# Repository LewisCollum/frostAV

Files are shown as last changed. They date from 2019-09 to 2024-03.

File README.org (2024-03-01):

Check out [[https://youtu.be/KNiY2aC7Y0c][youtube]], [[https://photos.app.goo.gl/i7FG5oYFuoorvApo9][images]], [[file:org/README.pdf][paper]]

** Getting Started
You do not need a vehicle to get started. As long as you have a
camera/webcam and a computer, you can run this application. This
project uses [[https://python-poetry.org/][Poetry]]. To run the application
#+begin_src bash
  poetry install
  poetry run frostav
#+end_src

Now in your browser, go to =localhost:5000=. If you have a camera
available (at =/dev/video0=) then you should see a livestream of the
camera. You can play around with the annotations provided in the
drop-down. For example, clicking the "signs" annotation will show a
box around detected signs (try holding a "stop" sign phone image in
front of the camera to see). Lane lines can be detected if you have
blue painter's tape held up to the camera (you may need to calibrate
the colors in code due to camera settings).

** I2C Communication
If you are running the application on a board that has i2c (e.g. RPi)
then install =smbus2= and the application will attempt to write JSON
steering and drive values to address =0x32=
#+begin_src bash
  poetry add smbus2
#+end_src

** Figures
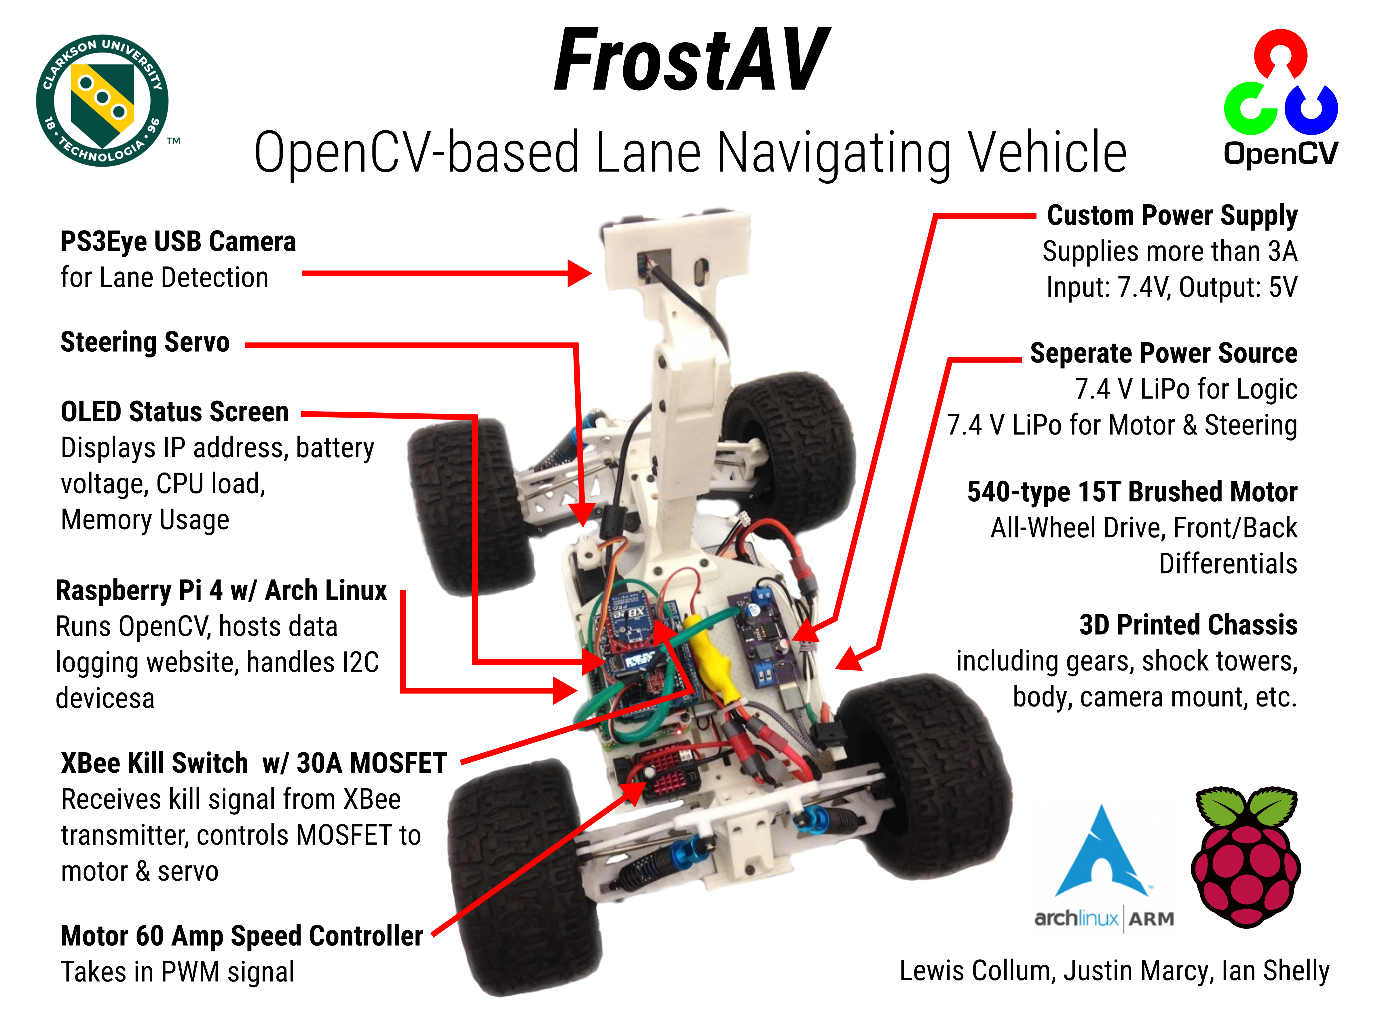
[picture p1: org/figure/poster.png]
 

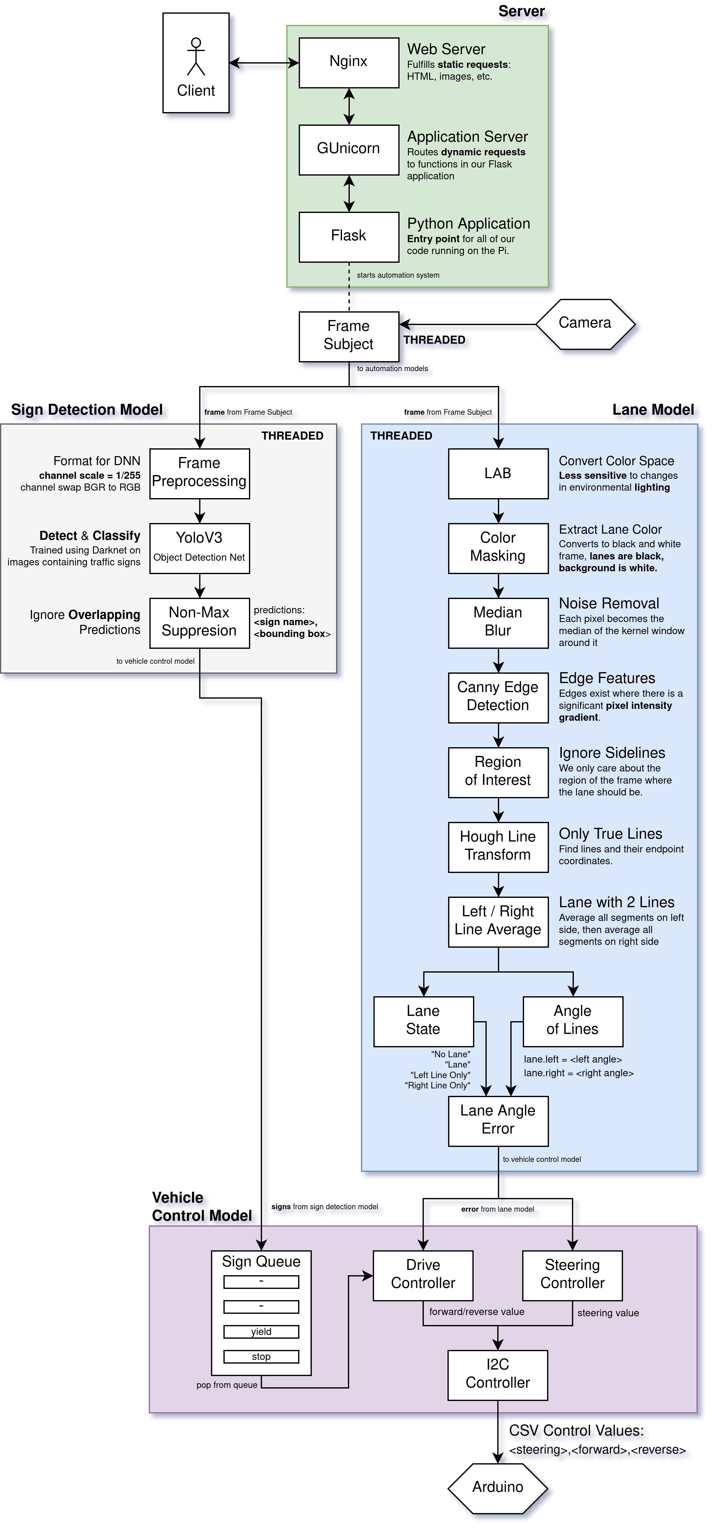
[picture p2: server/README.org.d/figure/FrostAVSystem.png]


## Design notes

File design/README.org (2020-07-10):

#+setupFile: ../org/latex_setup.org
#+title: Design
#+author: Lewis Collum

*** Power Supply (Designed by [[https://github.com/ishelly404][Ian Shelly]])
    Designed in KiCad, this power supply is meant to step down a *7.4V
    LiPo battery* to *5V*. It can output up to at least *3.5A*. In
    order to conveniently power USB devices (such as a Raspberry Pi),
    it has a 5V USB output socket.
    
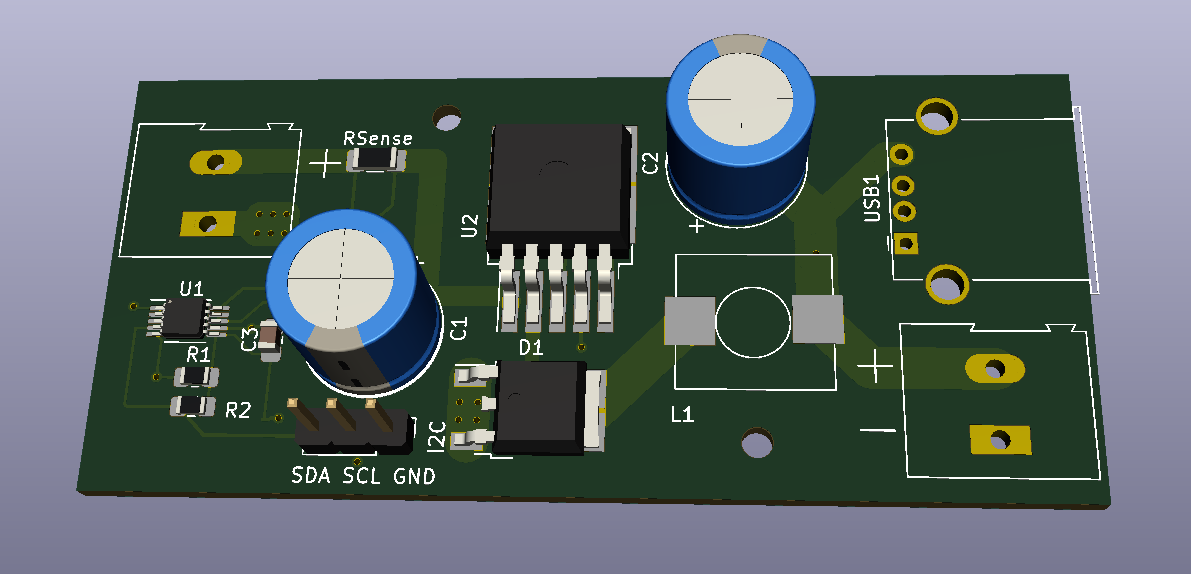
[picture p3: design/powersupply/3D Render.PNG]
    

*** Frost Schematic (Designed by [[https://github.com/ishelly404][Ian Shelly]])
    The main components on Frost include the Raspberry Pi 4, Arduino,
    OLED status display, and power supply. We also included an
    optional remote fail-safe switch that uses an XBee transmitter and
    receiver.
    
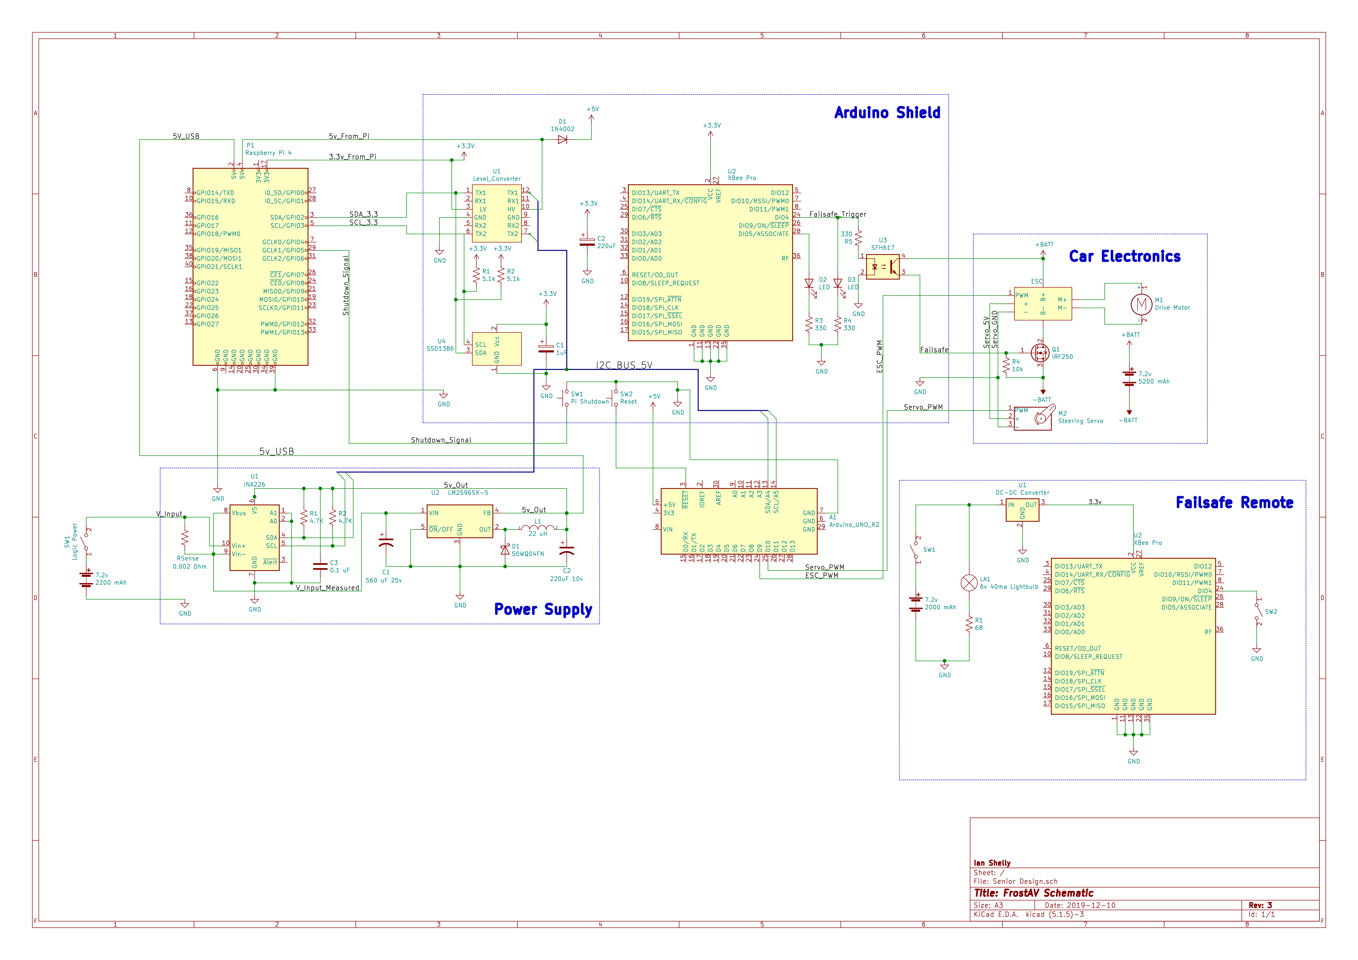
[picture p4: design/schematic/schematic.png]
    

*** 3D Printed Chassis
    The chassis is a remix of OpenRC on Thingiverse. Here is the most
    recent set of parts printed for mounting the Raspberry Pi,
    powersupply, and camera.

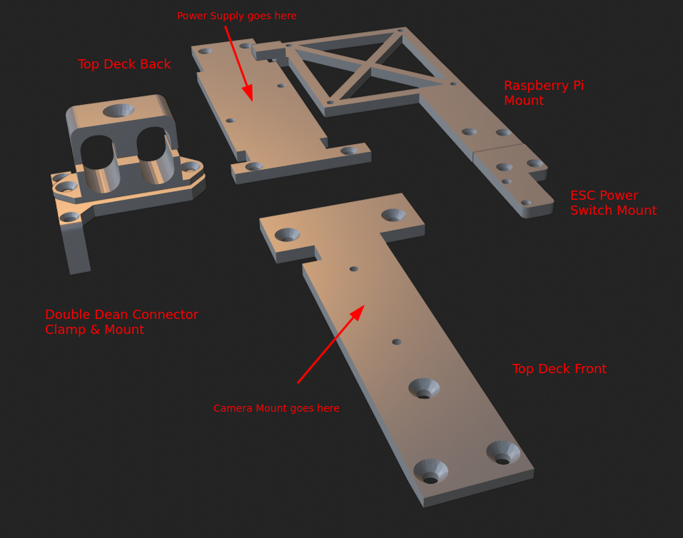
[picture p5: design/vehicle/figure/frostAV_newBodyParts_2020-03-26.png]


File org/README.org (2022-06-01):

#+setupFile: latex_setup.org 
#+title: FrostAV: Lane & Sign Detecting Tenth-Scale Vehicle
#+author: Lewis Collum

* Introduction
  Autonomous vehicles need to be able to follow a path, and react to
  environmental queues. The research that encompasses autonomous
  vehicles is not only useful for self-driving cars, but also within
  factory settings and places where transportation work can be
  automated.

  We 3D printed a vehicle, which holds a raspberry pi 4, Arduino, and
  a $5 USB camera, that is capable of following a lane and reacting to
  signs. This project demonstrates a real-time object detection
  network, a web server, and a lane detection system all
  simultaneously running on a $35 raspberry pi computer. In total,
  the cost of all parts on our vehicle is around $160.

  #+caption: 3D-printed tenth-scale chassis.
  #+attr_latex: :width 0.5\linewidth
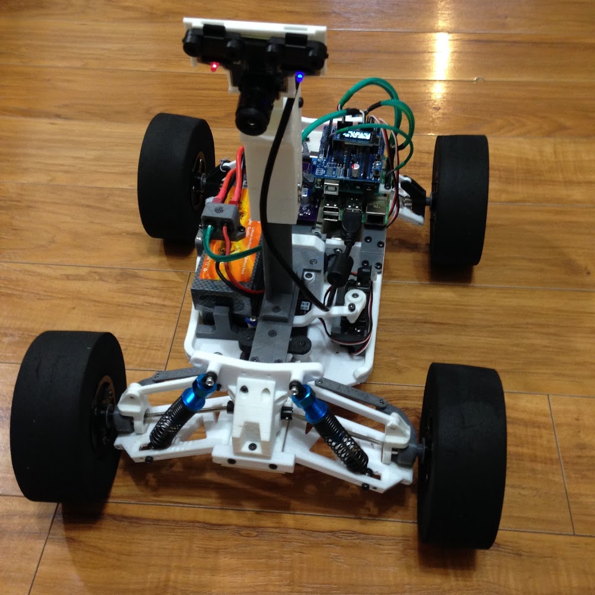
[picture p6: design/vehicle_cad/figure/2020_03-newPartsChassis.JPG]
  
  
* Vehicle Monitoring with a Web Server
  #+include: "../server/README.org" :lines "4-"
* Lane Detection
  #+include: "../server/autonomy/lane/README.org" :lines "4-"
* YOLOv3 Real-Time Sign Detection
  #+include: "../server/autonomy/sign/README.org" :lines "4-"
* Vehicle Control Model
** Control Value Packaging on the Raspberry Pi
   #+include: "../server/autonomy/vic/README.org" :lines "4-"
** Vehicle Interface Controller (Arduino)
   #+include: "../controller/README.org" :lines "4-"
* Vehicle Design                                                   :noexport:
  #+include: "../design/README.org" :lines "4-"
* Conclusion & Necessary Improvements
  We demonstrated the ability for a low-cost, $35 Raspberry Pi 4, to
  run a web server, lane detection system, and sign detection
  system. The method we used for calculating lane error has edge cases
  which make it inaccurate, (such as if the vehicle is outside the
  lane lines). This method would need to be improve the reliability of
  the vehicle navigation. Our sign detection model runs at about 1
  frame-per-second, which would need to be increased (through
  optimizations) if we want the vehicle to travel faster. Increasing
  the speed of the vehicle now, generally results in a sign being
  missed.

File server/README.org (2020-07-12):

#+setupFile: ../org/latex_setup.org
#+title: FrostServer
#+author: Lewis Collum

* Front-End: FPV Live Stream & System Statistics
  Everything starts with the server on the Raspberry Pi. On the server
  we have a website that allows us to monitor the vehicle from a
  client device. At the top, we have an FPV livestream (see figure
  [[fig-liveStream]]). Here we can examine the internals of our image
  processing system. The livestream is achieve by long-polling JPEG
  images from our main (Python) application to our website.

  #+name: fig-liveStream
  #+caption: Snapshot from the vehicle's website illustrating the FPV livestream. We can choose the type of frame we want to see (e.g. the LAB color-space frame) and the type of annotations we want to see (e.g. lane state and lane lines).
  #+attr_latex: :width 0.5\linewidth
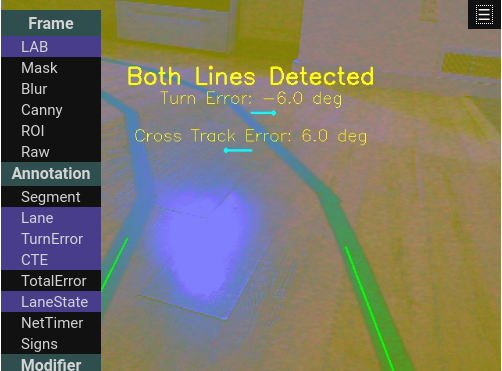
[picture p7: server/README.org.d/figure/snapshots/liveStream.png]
  

  We are also logging various system statistics, like load,
  temperature, and memory. Load is measured in number of jobs in the
  run queue averaged over a minute. Thanks to our custom designed
  power supply, we can also view power usage, battery voltage and
  current draw (see figure [[fig-stats_combined]]).

  #+name: fig-stats_combined
  #+caption: Snapshots from the vehicle's website illustrating Raspberry Pi system load, memory, and temperature, as well as power supply power, voltage, and current over time.
  #+attr_latex: :width \linewidth
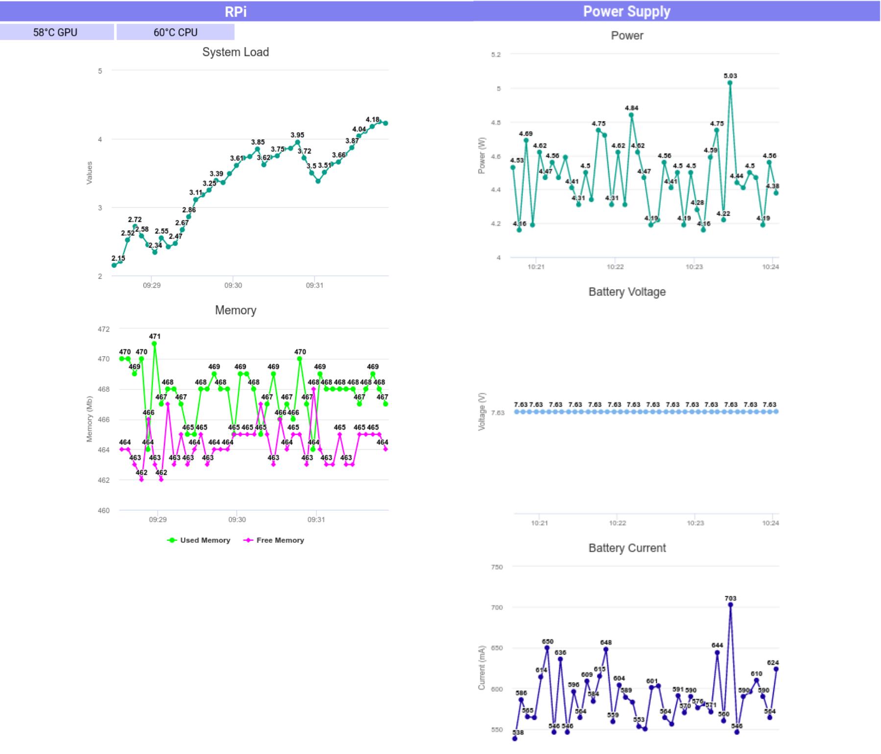
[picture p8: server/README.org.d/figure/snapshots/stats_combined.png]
  

* Server Overview: Flask, GUnicorn, and Nginx
  We use Flask, GUnicorn, and Nginx. Let's work our way down, from the
  website, to our application code (in python).

  *Nginx* acts as our web server, fulfilling requests from clients for
  static content from our website (e.g. HTML pages, files and
  images). Nginx forwards dynamic requests (e.g. all of the requests 
  that we want Python to handle) to GUnicorn, our 
  application server.

  *GUnicorn* ensures that Nginx and our Flask Python application can
  talk to each other. Ultimately, GUnicorn routes requests (passed
  through Nginx) to their corresponding function in our Flask
  application.

  *Flask* is a web [[https://en.wikipedia.org/wiki/Microframework][microframework]] in the form of a Python library. It is
  used in our Python application to provide functions that can receive
  requests, and return a response (e.g. sensor data). See figure [[fig-block_server]].

  #+name: fig-block_server
  #+caption: The client can see the server's website by typing in the server IP into a browser. All static requests, for the website, like html pages, styles and images, are handled directly by Nginx. Dynamic requests, for fetching system statistics for example, are routed to GUnicorn and then to our Flask application.
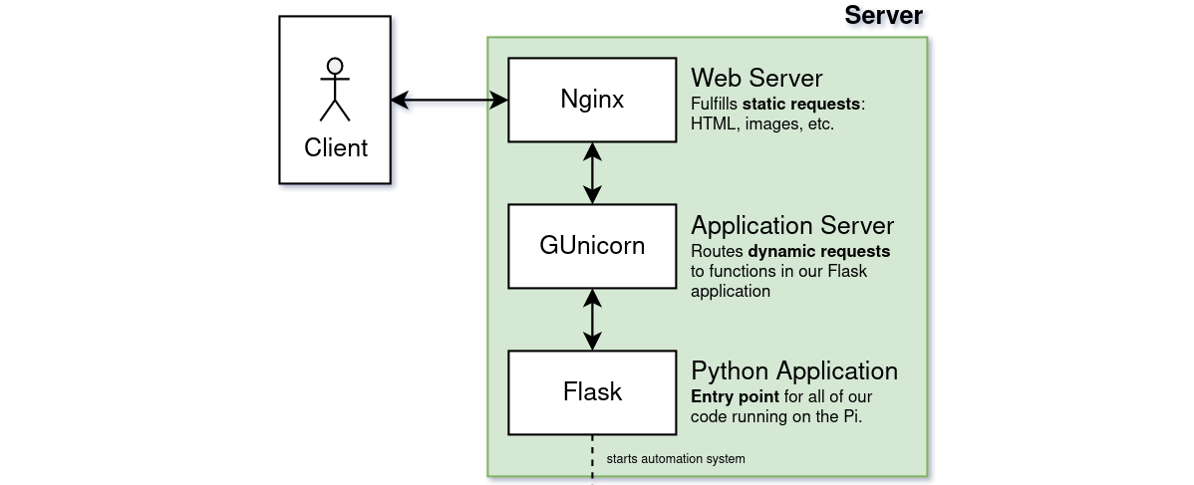
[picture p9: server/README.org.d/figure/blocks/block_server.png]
  

** Example: Real-Time Sensor Reading
  We have real-time plots on our front-end that request sensor
  data. Eventually, we expect to receive this sensor data from a URL
  of our choice (e.g. "/sensor_reading"). These requests are sent to
  Nginx, which are then passed to GUnicorn (since they are dynamic
  requests). GUnicorn sends the requests to a function in our python
  application that is registered for the formerly mentioned URL. The
  function is registered with the given URL using Flask. This function
  has code to get sensor data from the underlying linux system
  (typically, by reading a sensor file or running a shell
  command). Finally, the function returns a response which contains
  the sensor data.
  
** Resources :noexport:
   - https://en.wikipedia.org/wiki/Multitier_architecture
   - https://serverfault.com/questions/331256/why-do-i-need-nginx-and-something-like-gunicorn
   - https://www.nginx.com/resources/glossary/application-server-vs-web-server/
   - https://flask.palletsprojects.com/en/1.1.x/api/#flask.Flask.route

# * Server Started at Boot
# Stuff about systemctl

# * Developing with Flask
# export FLASK_ENV=development
* Installing Nginx, Flask, and GUnicorn
  Since we are using Arch Linux ARM on our Pi, we used Arch Linux's
  package manager ~pacman~ for Nginx and Gunicorn. We used ~pip~ to
  install Flask.

  #+begin_src bash
sudo pacman -S nginx
sudo pacman -S gunicorn
sudo pip install flask
  #+end_src

* Starting the Server the First time
  For ease, this repository was cloned on our Raspberry Pi to the user
  directory (e.g. "/home/alarm"). In the =frostServer/config= directory,
  there is a setup script[fn:asSudo] which does the following:
  
  1. links the frostServer.service to the system directory;
  2. links the frostServer.nginx config file to nginx's enabled-sites
     directory;
  3. enables both the nginx and the frostServer services;
  4. starts both services.
  
  Now, on a computer connected to the same WiFi as our Pi, we can type
  the IP of the Pi into the browser search bar (e.g. "192.168.0.106")
  and the Frost website appears. Since we enabled the server service,
  the server will start at boot without any user intervention.

* Automation System
  The server is also responsible for starting the automation
  system. The automation system begins in code with a Frame Subject
  (see README.org.d/figure [[fig-frameSubject]]), which is a simple object that
  captures images, or as we will call them, frames, continuously from
  the camera. We have two models which take a copy of each frame: the
  Lane Model, and the Sign Detection Model. Since these models are
  both computationally expensive, we set them up to process the frames
  from the Frame Subject in their own thread. This ensures that other
  parts of our application are not slowed down by these models. It is
  also important to note that these models are fully independent from
  each other. That is, one model does not affect the result of the
  other model.

  #+name: fig-frameSubject
  #+caption: Illustrates the Frame Subject being started (as a thread) from the server (Flask) application code, from which, the lane and sign detection models can pull camera frames.
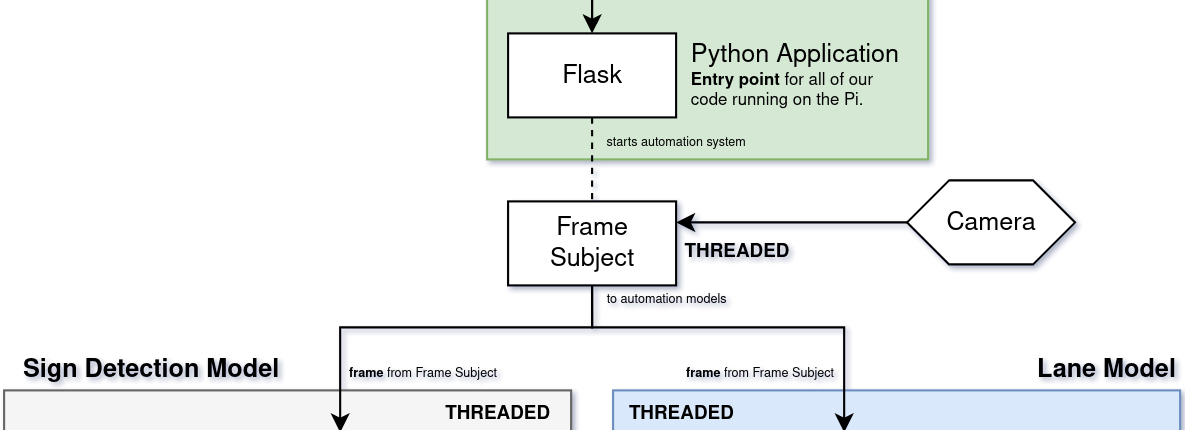
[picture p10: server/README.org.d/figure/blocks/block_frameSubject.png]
  
  
* Footnotes :ignore:
[fn:asSudo] The setup script should be run as =sudo=.

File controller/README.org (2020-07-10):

#+setupFile: ../org/latex_setup.org
#+title: Vehicle Interface Controller (VIC)
#+author: Lewis Collum

** Overview
  We are using an Arduino Uno to take in i2c steering and drive values
  to control the vehicle's steering servo and electronic speed
  controller (ESC). We refer to the Arduino as the Vehicle Interface
  Controller (VIC).

  The VIC is programmed in C++ (not using Arduino's packages). This
  gives us control over the implementation details of utilities like
  strings, pwm, usart, and i2c. Note that this decision was made for
  our own academic curiousity.

** Application Makefiles
  The VIC uses GNU Makefiles. We have modularized the makefile
  process, such that when starting a new application file (i.e. a
  source file which contains =main=) the makefile to build the
  application only needs to contain

  #+begin_src makefile
TARGET = <name of your application>
ROOT = ../..
include $(ROOT)/mk/all.mk
  #+end_src

  where =ROOT= is the directory that contains the =mk= directory.

** Making a New Application 
  We have included a bash script in =app= called =createNewApp=. To
  make a new application, we can go to the app directory and run
  
  #+begin_src bash
  ./createNewApp <name of application>
  #+end_src
  
  This script ensures there are no existing applications and if that is true:
    1. will make a directory with the same name as our application;
    2. will make a =cpp= source file with the name as our application;
    3. will create a Makefile, filled with everything necessary to
       build our application.
    
** Flashing the Arduino
   To flash the Arduino, we go to the directory of an application (in
   the =app= directory), and then we run =make flash=. The build files
   are exported to the =app/build= directory.
  
** Serial Interface
   To communicate with the Arduino, via Serial, we use =picocom=, a
   linux terminal utility. As part of our modular makefile system, we
   can open =picocom= by going to the directory of an application (in
   the =app= directory), and running =make com=.

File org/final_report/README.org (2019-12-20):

#+title: FrostAV Final Report
#+options: toc:t num:t
#+latex_header: \usepackage{development}
#+bind: org-latex-minted-options (("bgcolor" "code"))
#+bind: org-latex-image-default-width "\\linewidth"

** Requirements Evaluation
*** Problem Domain Requirements
The main problem-domain requirements for this project are:
   1. Given a _lane_, the car must travel approximately parallel to it,
      such that the car stays within its _boundaries_ consistently,
      and, if the car is to accidentally leave it, it promptly
      returns.
   2. Given a _corner_, the car must turn, continuing from the car’s
      current _lane_ to the next, such that the car stays within its
      _boundaries_ consistently, and, if the car is to accidentally
      leave it, it promptly returns.
   3. Given an _obstacle_, the car must stop until it is moved
      further from the car, or it is removed from _circuit boundaries_.
   4. Given a _sign_, the car must respond to the event provided by it.
   5. Given a _circuit_, the car must complete a full loop.

   #+caption: An example _circuit_ which the car must navigate through.
   #+attr_html: :width 300px
   #+attr_latex: :width \linewidth/2
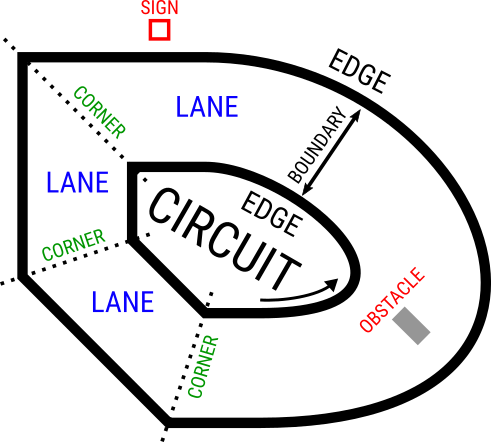
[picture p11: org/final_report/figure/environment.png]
   

The completed project is fully capable of meeting requirements 1, 2 and 5 and is unable to meet 3 and 4. The car can successfully navigate a straight path and recover from small excursions outside of the lane boundaries. It can also navigate corners and complete a circuit. Obstacle detection and sign detection was never implemented due to a lack of time.

*** Control System and Control Module Requirements
For the control system and control modules, the following requirements apply:
    The Control System shall:
   1. Interface with vehicle peripherals, such as, motors, servos,
      batteries, etc.
   2. Be the only system coupled to the vehicle. 
   3. Have a subset of Control Modules for each peripheral in need
      of control.

    Each Control Module shall:
   1. Encapsulate a single purpose, such that, one controller controls
      a single peripheral.
   2. Couple to a peripheral electronically, not mechanically.
   3. Be able to communicate with other controllers via a wired bus.
   4. Be able to communicate with non-controllers that depend on it,
      via a wired bus.
   5. Communicate with other controllers and non-controllers via a
      single shared wired bus.

All the control system and control module requirements were met, except for the requirement that each control module must control a single peripheral. In the final design, the ATMEGA328 is used for both servo and throttle control instead of having a separate module for each. Otherwise, the control system was able to successfully interface with the vehicle peripherals using control modules, and the control modules share a single I2C bus. All control modules can communicate with the Raspberry Pi, which runs the main control system, and with each other (even though this capability was not utilized for the final design).

*** Autonomy Requirements

The vehicle’s autonomy system shall:
   1. Not be directly coupled to the Vehicle Interface
   2. Be able to fit on the vehicle.
   3. Allow the vehicle to navigate without user interaction.
   4. Be able to communicate with the Control System.
The final design is capable of meeting all the autonomy requirements. The autonomy system can communicate with all modules that make up the control system, including communicating with multiple modules in quick succession. The system is not directly coupled to the vehicle interface, instead performing all vehicle functions using control modules. The system fits on the vehicle and allows the vehicle to navigate autonomously.

*** Vehicle Interface Requirements

The vehicle interface shall:
    1. Include a way for the vehicle to be turned on and off, such
       that, the vehicle receives no power to the _drive system_ or
       _logic_ when off.
    2. Include a way for the vehicle to have its _logic_ turned on,
       while the _drive system_ is off.
    3. Provide a battery peripheral that powers the _logic_.
    4. Provide a battery peripheral that powers the _drive system_.
    5. The total power consumption of the _logic_ and _drive system_
       cannot exceed the maximum capacity of the battery
       peripheral(s).
    6. Provide a peripheral that moves the vehicle.
    7. Provide a peripheral that steers the vehicle.
    8. Provide an electronic interface from each peripheral.

All vehicle interface requirements were met with the final design. The design meets requirements 1 and 2 with a power switch on the logic battery, and a power switch and remote cutoff on the drive battery. This allows the logic to be powered independently of the drive system. Requirements 3 and 4 are met with the inclusion of the logic and drive batteries as well as the logic power supply. The batteries and power supply allow all the logic and drive system modules to be powered. 

Requirement 5 is met by ensuring that the maximum power draw won’t exceed the batteries maximum rating. All of the batteries used in this design are rated at 30C or greater, which is a measure of a batteries maximum discharge rate. For the 5200 mAh drive battery, a 30C rating corresponds to a maximum output of 156 A. The ESC used to power the drive motor and servo is rated for a maximum of 60A, so the maximum potential current draw is well within the battery’s capabilities. The logic battery, which has a capacity of 2200 mAh and a discharge rating of 30C can supply a maximum of 66A. Since all logic is powered by the power supply (which has a current limiting function) the maximum current drawn from this battery will never exceed 3A. 

Requirements 6 and 7 are met by the ATMEGA328, the motor, ESC and steering servo. The ATMEGA328 controls the servo and ESC, and the ESC regulates the motor’s speed. These components allow the vehicle to be steered and moved by the autonomy system. Each peripheral also has an electronic interface. The ATMEGA328 communicates with the autonomy system, which is running on a Raspberry Pi using the I2C bus. The voltage and current draw of the logic battery are measured using the INA226 power monitoring chip built into the power supply and communicated to the autonomy system over the I2C bus.

*** Wireless Interface Requirements
    The Wireless Interface shall:
    1. Allow for wireless tunneling (e.g. via SSH)
    2. Be able to access a server.
    3. Provide bi-directional communication.

All of these requirements for the wireless system are met in the final design, using the Raspberry Pi 4’s integrated WiFi. The Wifi connection allows for SSH tunneling as well as providing a HTTP server. The system is also capable of connecting to a server using SSH tunneling. The Wifi is also fully capable of bi-directional communication.

** Additional Capabilities

During the development of the vehicle, a few additional capabilities and features were able to be implemented.

*** Status OLED Display

   #+caption: OLED display showing parameters.
   #+attr_html: :width 300px
   #+attr_latex: :width \linewidth/2
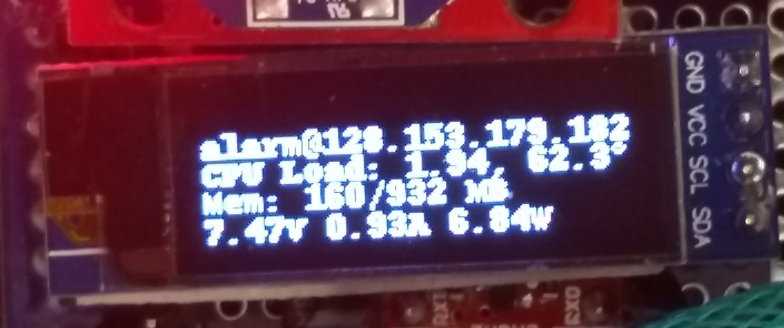
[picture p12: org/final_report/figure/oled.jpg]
   

A SSD1306 OLED display module was added to the design towards the end of Milestone 4, which allows easier monitoring of the Raspberry Pi and battery parameters. The display shows the current IP address of the Pi, the CPU load and temperature, memory usage, and the voltage, current draw and power use from the logic battery. 

This display has been useful in the development of the system because it allows important parameters to be monitored easily. Since the Clarkson University Wifi uses DHCP addresses, the Pi’s IP changes periodically. The IP is needed for accessing SSH and the Pi’s webserver so this is a very useful parameter to have. The voltage monitoring serves as a low battery indication for the logic battery.

*** HTTP Status Monitoring

   #+caption: An example _circuit_ which the car must navigate through.
   #+attr_html: :width 300px
   #+attr_latex: :width \linewidth/2
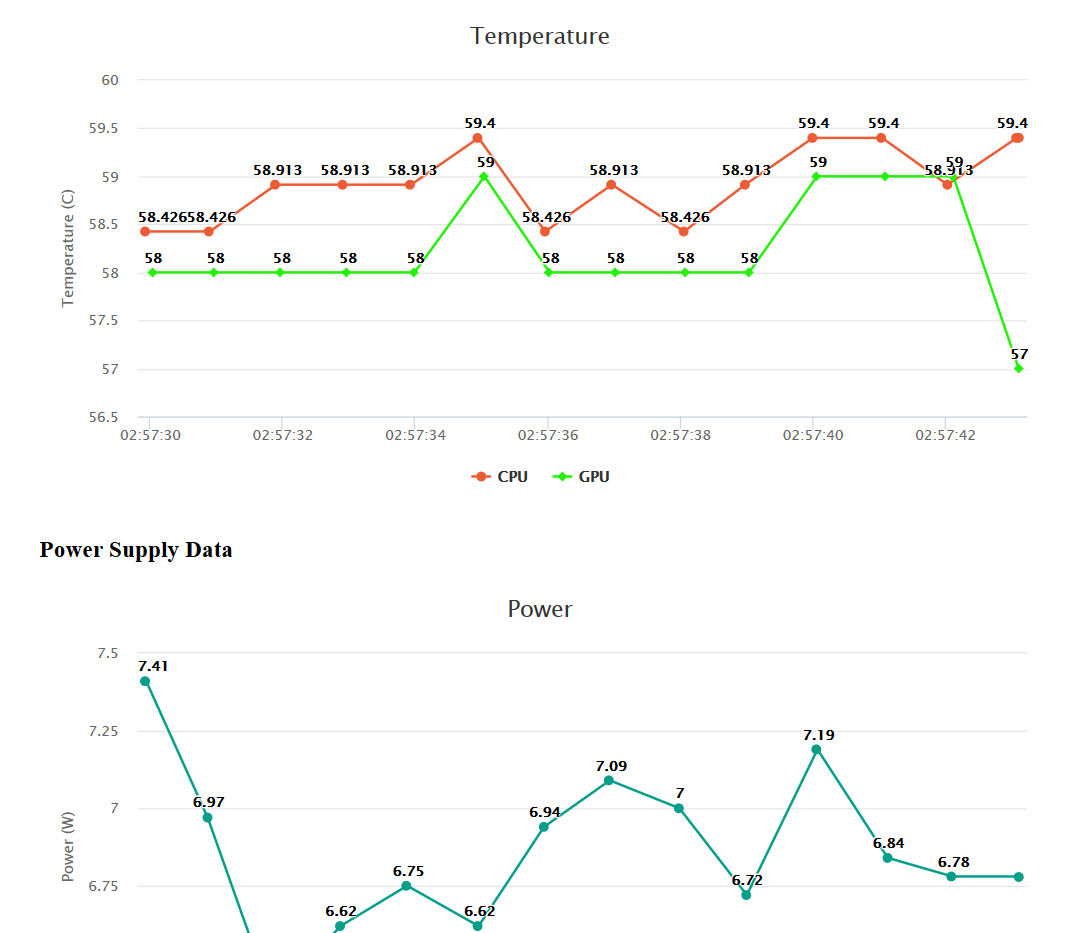
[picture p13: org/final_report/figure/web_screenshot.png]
   

Similar to the OLED display, a web server was implemented on the Pi to monitor various parameters. The parameters monitored are the Pi’s CPU load, memory use, CPU and GPU temperature, and power, voltage and current from the logic battery. These parameters are graphed using JavaScript and the values are retrieved with PHP. The graphs update every 10 seconds and display the last 20 values. The webpage is accessed at the Pi’s IP address.

This feature allows various parameters to be measured and allows the easy identification of trends in these values. The function of this webpage is like the OLED display, in that it’s useful for the development of the system. This allowed for the identification of thermal throttling on the PI during testing.

*** Remote Motor/Servo Shutoff

   #+caption: Shutoff remote control.
   #+attr_html: :width 300px
   #+attr_latex: :width \linewidth/2
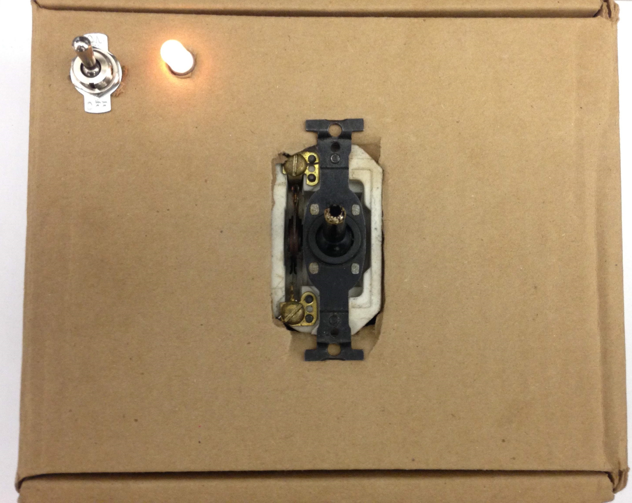
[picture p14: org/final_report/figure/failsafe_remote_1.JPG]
   

A remote shutoff system was implemented using Xbee radio modules and an IRF250 power MOSFET. The MOSFET cuts power to the motor speed controller and servo when the switch on the remote control unit is flipped. This system allows the car to be stopped remotely if it were to go out of control. The system is designed so that any failure will disconnect power to the motor and servo. If the Xbee on the car side loses signal or power, it will stop the motor.

** Unique Innovations
*** Custom Power Supply

   #+caption: Power Supply complete.
   #+attr_html: :width 300px
   #+attr_latex: :width \linewidth/2
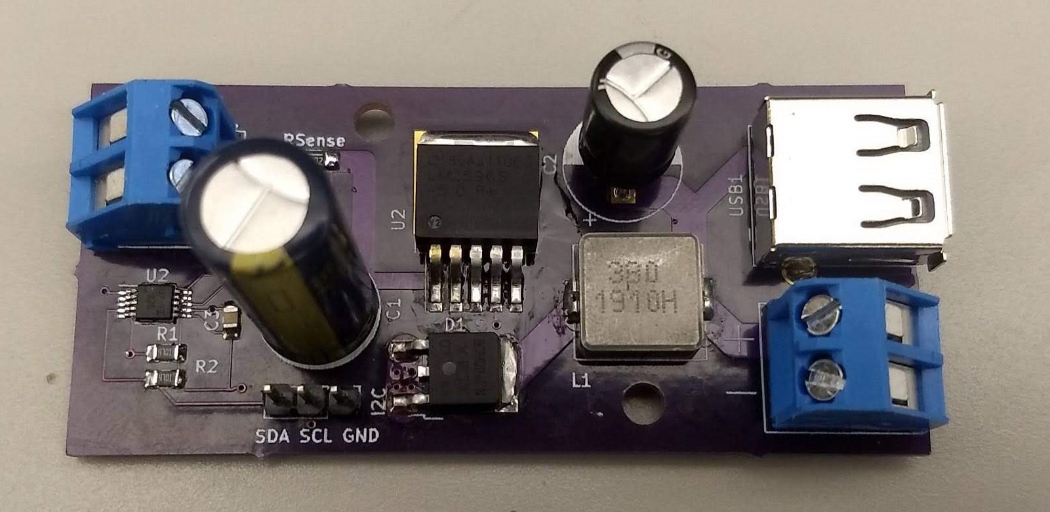
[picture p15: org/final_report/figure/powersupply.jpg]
   

A custom power supply was designed to convert the 7.2v from the LiPo batteries to 5v for powering the car’s logic systems. The power supply is also capable of measuring battery power, voltage and current. The power supply is implemented using a LM2596-5.0 buck regulator IC, and an INA226 power monitoring IC. The power supply can supply the Raspberry Pi 4, which requires 5V at 3A as well as the ATMEGA328 board and other accessories. 

   #+caption: Power Supply schematic.
   #+attr_html: :width 300px
   #+attr_latex: :width \linewidth/2
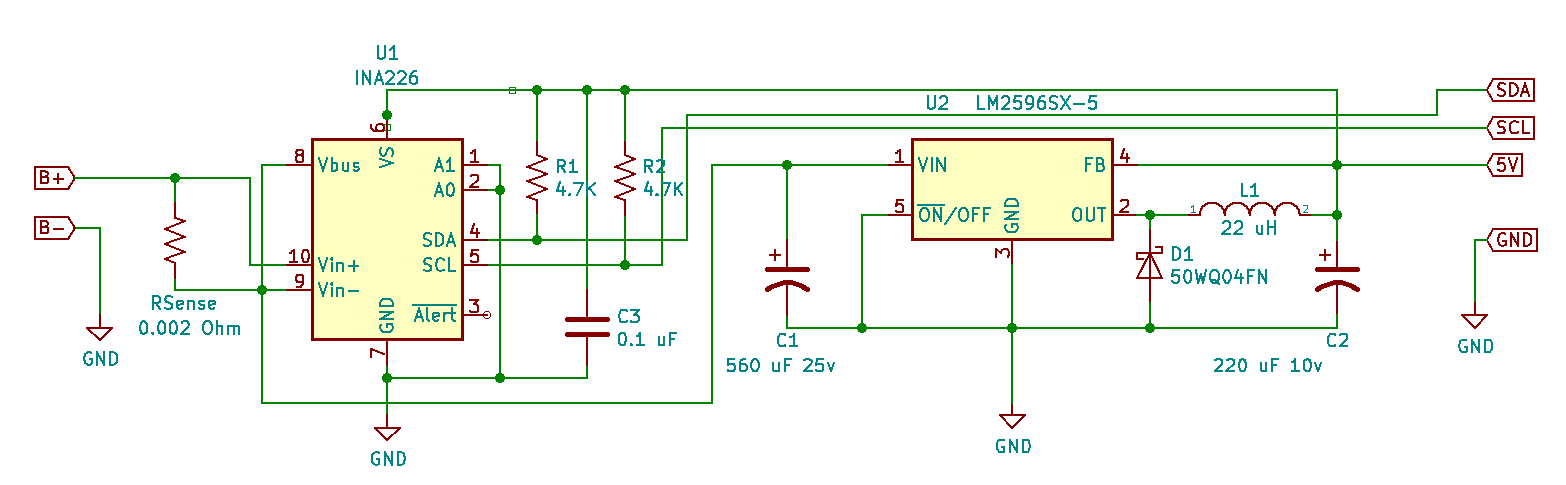
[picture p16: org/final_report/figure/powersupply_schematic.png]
   

For the design of the power supply, a TI LM2596-5.0 “Simple Switcher” buck converter was chosen because of its efficiency, 3A output and ability to accept an input voltage as low as 7v. Originally a LM7805 based design with a bypass transistor was considered, but it would have been much less efficient. This would have reduced battery runtime and require a large heatsink which would have added weight. The values of L1, C1 and C2 were chosen based on the LM2596’s datasheet. The output current was assumed to be 3A, and the maximum input voltage as 12v (providing the ability to operate using a 3 cell LiPo if needed). 

The inductor L1 is a Bourns SRP1038A-220M which is shielded and has a saturation current of 5A. Since the components are in close proximity a shielded inductor is needed to prevent EMI from affecting the feedback line of the LM2596 (Pin 4) as well as the INA226 and I2C lines. The capacitors C1 and C2 are Nichicon aluminum polymer electrolytics, which have a very low (30 mΩ) ESR (equivalent series resistance). Low ESR is critical in a buck converter design because of the high current transients created by the switching. A low ESR allows the capacitor to charge and discharge faster to react to these transients. Diode D1 is a 50WQ04 Schottky diode which was used because of its fast switching time and low voltage drop.

For the power measurements, a TI INA226 current and power monitor was used because of its Linux driver support. The INA226 communicates with the Raspberry Pi over I2C, with R1 and R2 functioning as pull-up resistors. The INA226 measures current using a shunt resistor and measuring the voltage across it. The resistor’s value is programmed in at startup and from there an accurate current measurement can be taken. The shunt resistor Rshunt is a 0.002Ω 1% resistor as recommended in the INA226 datasheet.

   #+caption: Power Supply PCB layout.
   #+attr_html: :width 300px
   #+attr_latex: :width \linewidth/2
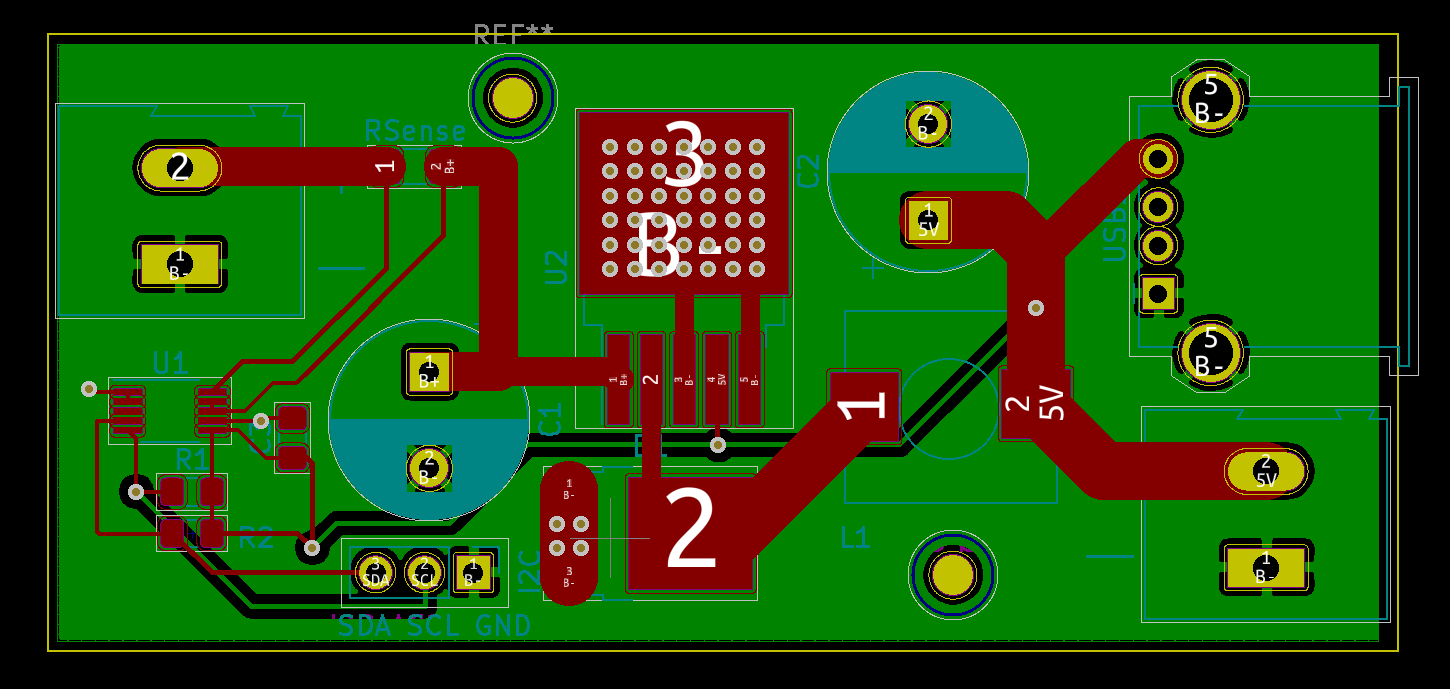
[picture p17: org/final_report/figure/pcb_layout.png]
   

Since the buck converter operates at a frequency of about 150kHz and used many surface mounted components, a custom PCB (printed circuit board) was designed using KiCad. The power supply was originally constructed on a protoboard (without the INA226 power measurement IC) and while it was somewhat functional it had stability issues and the output was limited to about 2A at 5V. The custom PCB eliminated all of these issues as well as creating a more mechanically robust design. 

High currents and frequencies are present in the power supply, so a ground plane design was used for the PCB. The back side of the board (shown in green) is copper filled and used as the ground connection for all components. Components on the front side of the board are connected to the ground plane using through-hole vias, which are holes drilled and electroplated through the board. The ground plane is also used as a heatsink for the LM2596 buck controller IC. Multiple vias were placed on the heatsink pad of the device to help conduct heat and serve as a ground connection. Thicker traces and shorter trace lengths are used for high current paths.

   #+caption: Power Supply PCB Before Assembly.
   #+attr_html: :width 300px
   #+attr_latex: :width \linewidth/2
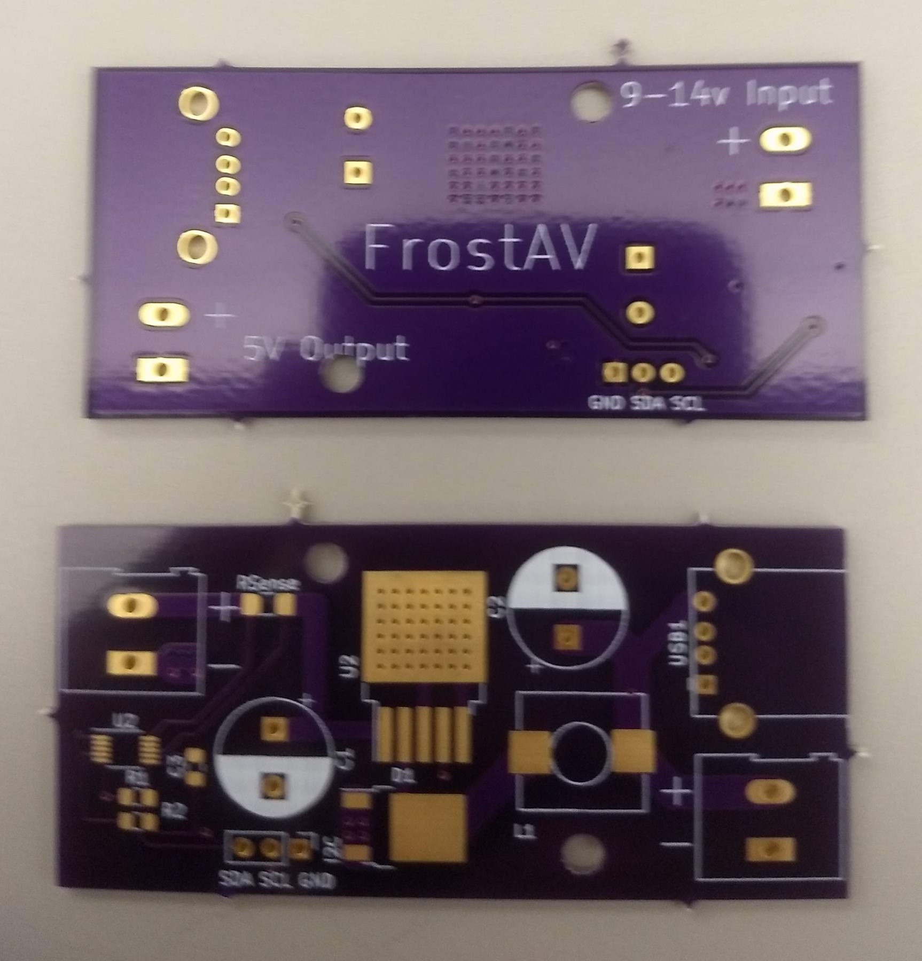
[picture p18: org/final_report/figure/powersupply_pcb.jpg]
   

The PCB’s were manufactured by OSHPark, and all components were hand soldered. The larger components such as the inductor, diode and buck regulator were hot air soldered and the smaller components were soldered using a fine soldering iron tip. Solder wick was used to remove excess solder and a few solder bridges between INA226 pins.

*** Reading Power Supply Data in Linux

To measure the battery voltage and power consumption, a TI INA226 power monitoring IC was added to the power supply design. Linux includes a driver to read data from this device, and in order to use it on the Raspberry PI configuration changes need to be made. Since the Raspberry Pi doesn’t support hardware autodetection on any interface except USB, a system known as device tree is used to describe the system’s hardware configuration. The device tree provides information on all the system’s hardware, such as the addresses, registers, driver parameters and other information. The device tree is read by the Linux kernel at boot and then loads the required drivers and their parameters.

#+BEGIN_SRC emacs-lisp
/dts-v1/;
/plugin/;
/ {
	fragment@0 {
		target = <&i2c1>;
		__overlay__ {
			status = "okay";
			ina226@40 {	
				compatible = "ti,ina226";
				reg = <0x40>;
				shunt-resistor = <2000>;
			};
		};
	};
};
#+END_SRC

To add support for the INA226 a device tree overlay needed to be created to insert it into the system’s device tree. The contents of this file are shown above. The bus that the INA226 is attached to is defined with ~target = <&i2c1>~, the driver is set with ~compatible = 'ti,ina226'~ and the address with ~reg = <0x40>~. The shunt resistor value is set with ~shunt-resistor = <2000>~, with the resistance value in micro-ohms. The shunt resistor value is the resistance of the current shunt connected to the INA226, which is used for current and power calculations. In this case the current shunt’s resistance is 0.02Ω. The device tree overlay is enabled in the Raspberry Pi’s ~/boot/config.txt~ file. 

Once the driver is set up the voltage, power and current measurements can be accessed by any Linux program. The ~sensors~ utility can be used to display these values.

** Problems

*** Vehicle Issues
**** Motor and Drivetrain Issues

Originally, the vehicle was intended to use a brushless motor and speed controller. There were issues with the brushless speed controller, so a brushless motor and speed controller were used instead. There were also issues getting the motor and center gear to mesh correctly, the motor kept shifting out of position. This was fixed by tightening the motor mounting screws. The 3D printed driveshaft coupling pieces broke a few times and the original center gear was warped. These pieces were reprinted in carbon fiber PLA. 

**** Mounting and Fitment Issues

The original steering servo, a Hitec HS-422 didn't fit in the steering servo mount. Since the base plate of the car was already printed, it couldn't be enlarged to fit the servo without the screw holes not lining up. Eventually another servo was found which was small enough to fit the mount. Another issue was encounterd when the Raspberry Pi 2 was replaced with a Raspberry Pi 4. The mounting holes on the Raspberry Pi are 1.9 mm in diameter but the smallest mounting hardware was 2 mm. The holes were drilled out to fit the mounting hardware.

Another issue with the car was that since the body was slightly narrower than the original plans, the steering tie rods were slightly longer than needed. This caused the front wheels to angle in slightly. Shorter tie rods were printed but the wheels still had the same issue. Reprinting them again a few mm shorter would solve this issue.

*** Power Supply Issues

There were a few issues with the power supply during the development process. The original prototype of the power supply was built on a protoboard using through hole components. The inductor originally used for this design had the wrong value (68 uH vs 22 uH). Since this was a large toroidal inductor, the problem was resolved by taking turns off th inductor core until it measured at 22 uH. This iteration had stability issues where the power supply output voltage would randomly drop, even with no load. This iteration also had a max output current of about 1.5A. These issues were determined to be caused by the long lead lengths and EMI problems from the protoboard construction. 

There was also a few issues with the second version mainly related to PCB layout. The USB port’s power and ground lines were swapped, assuming it was top mounted. The solution to this problem was to desolder the port and install it upside down on the bottom of the board. Another issue was that the negative lead of the input capacitor (C1 on power supply schematic) was not connected to the ground plane, or anything else. The solution to this was to scrape off some solder mask from the ground plane and bridge the connection with solder.

*** Remote Shutoff Issues

A few problems were encountered with the remote shutoff system. With the original circuit, a JFET was used to drive the power MOSFET's gate. Sudden throttle changes and using the braking feature would cause the Xbee to reset, thus cutting power to the ESC. A decoupling capacitor was added to the Xbee power terminals, but this didn't solve the issue. The JFET was replaced with an optocoupler which electrically isolated the Xbee and power circuits. This solved the resetting issue, but the Xbee would still shut off ESC power after 60 seconds. This turned out to be a tim eout issue because the remote Xbee would only transmit when the switch's position was changed and the receiving ESC would time out after not receiving any transmission. After changing the Xbee programming to transmit every 10 ms this issue was solved.

* Test Results
*** Autonomous Driving Tests
   #+caption: Vehicle navigating the wide section of test track.
   #+attr_html: :width 300px
   #+attr_latex: :width \linewidth/2
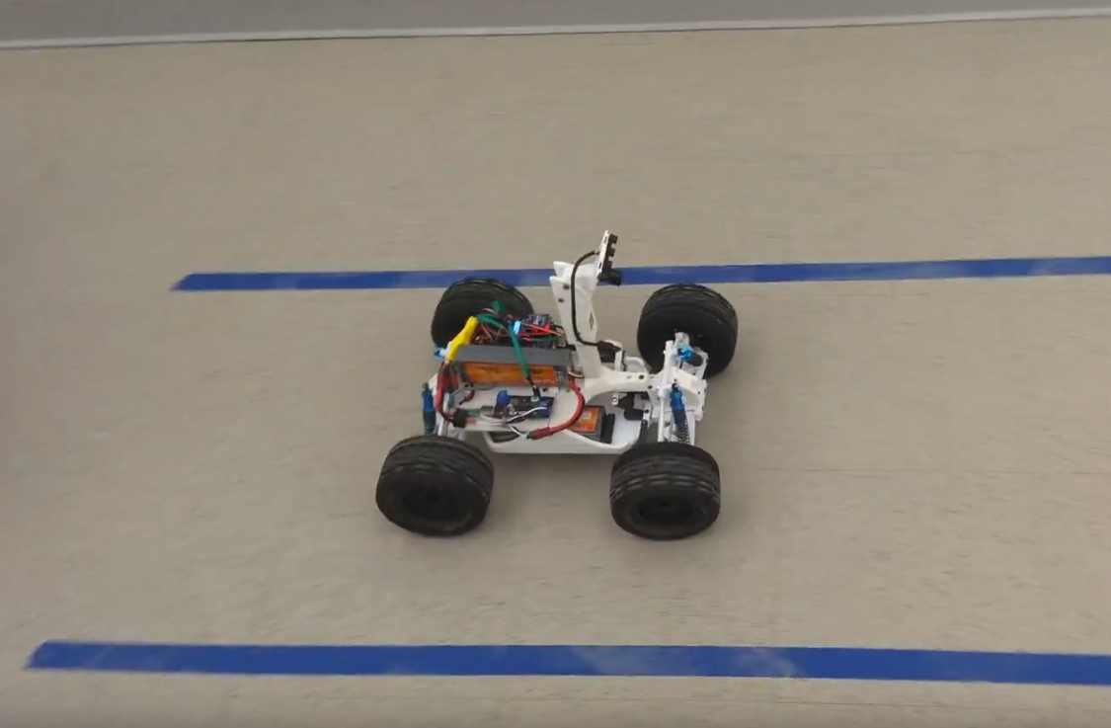
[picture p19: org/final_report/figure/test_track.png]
   

In order to test the car’s autonomous driving capabilities, a test track was constructed. The lines for the testing track were marked with two parallel strips of blue masking tape. Two different widths were used for the track, 12 and 24 inches apart (based on the 12”x12” floor tiles). 
   #+caption: Vehicle navigating the narrow section of test track.
   #+attr_html: :width 300px
   #+attr_latex: :width \linewidth/2
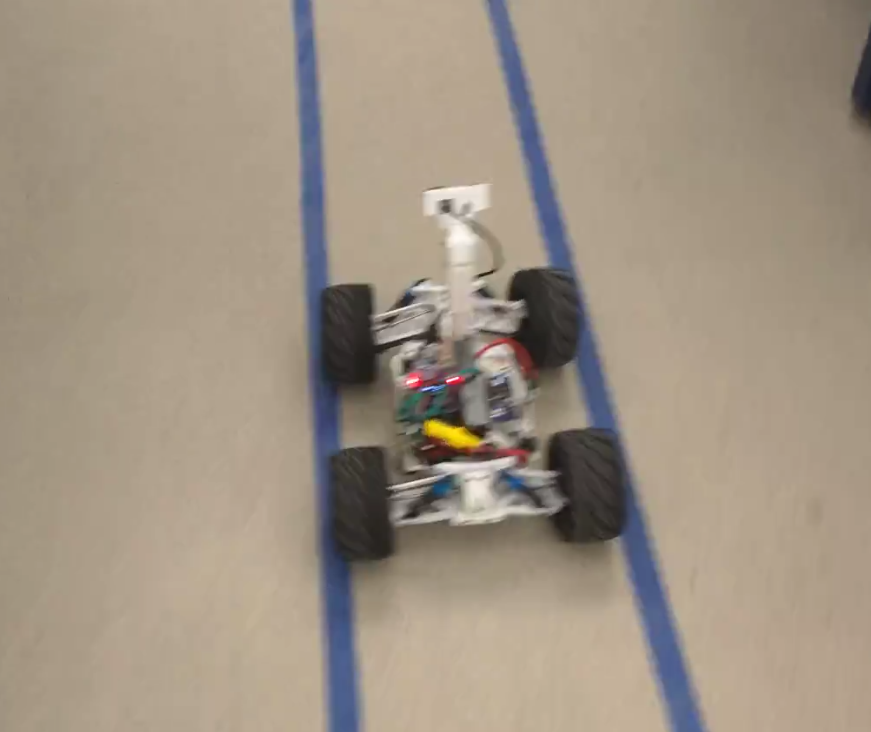
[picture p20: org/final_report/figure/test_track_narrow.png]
   

The vehicle was able to successfully navigate the test track multiple times. It did leave the track a couple of times during testing, and with more time these issues could be resolved. The vehicle could handle corners and varying track widths, as well as merging from the wide track to the narrow one. 
  
*** OpenCV Lane Detection Testing Results
*** ATMEGA328 Firmware Testing Results

The ATMEGA328 firmware was tested in two parts, first testing the I2C interface itself and then verifying that the servo and throttle could be controlled using I2C commands. While the ATMEGA328 was originally intended to function as a PID controller as well, this function was eliminated due to a lack of development time.

For the first part of firmware testing, the ATMEGA was tested to ensure it would respond to its own I2C address. The ATMEGA was connected to the Raspberry Pi’s I2C pins through a level converter, and the Linux utility “i2cdetect” was used to scan for I2C devices. This utility tries each possible I2C address, and shows the addresses of the devices that respond. An example of this is shown in figure 1.1.2-1, with the ATMEGA using I2C address 0x32.
#+caption: Results of running ‘i2cdetect’ command while three devices were connected to the Raspberry Pi’s I2C bus.
   #+attr_html: :width 300px
   #+attr_latex: :width \linewidth/2
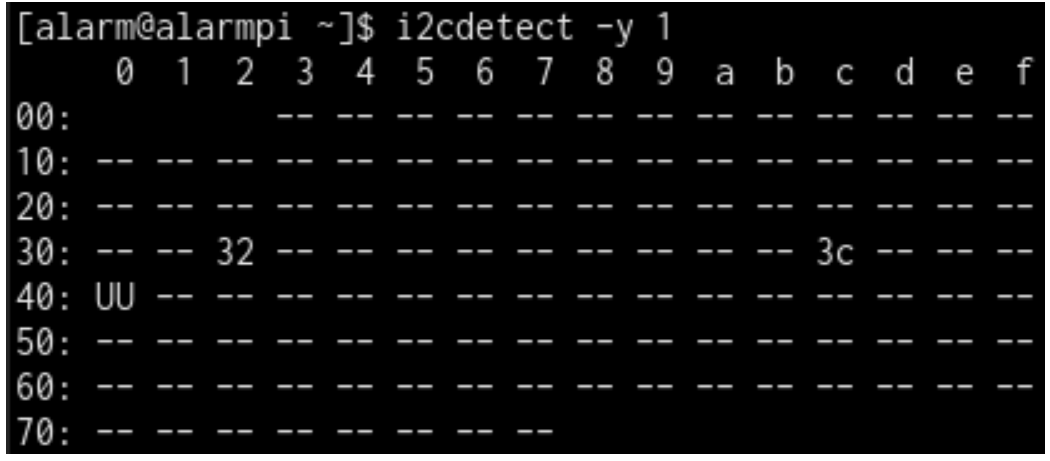
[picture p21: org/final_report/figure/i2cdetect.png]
   

During this testing, a few issues with the I2C controller were encountered. The first time “i2cdetect” was ran, the results were as shown above, with the ATMEGA responding to its own address and the other devices were able to respond as well. The second time it was run the ATMEGA held the data line to ground and no I2C communication was possible. When the ATMEGA was reset, the same issue would occur with a correct response the first time and a failure for all subsequent tries. This issue was found to be in an open source I2C library used on the ATMEGA which was not properly clearing the I2C interrupt bit. Once this issue was resolved the ATMEGA reliably responded to its I2C address.

For the next phase of testing the ATMEGA firmware was modified to print all data received over I2C to the USART. A small C++ program called “i2c-test” was written to send data to the ATMEGA from the Raspberry Pi. When this test was performed, there was a minor issue with the ATMEGA firmware expecting a newline character (0x12) but “i2c-test” sending a null character (0x0) instead. Once this was fixed, the firmware performed as expected with all data sent over I2C being printed to the USART console.
The final stage of testing was done to ensure that throttle and servo control over I2C were possible. The car was placed onto a stand and the motor speed controller and servo were connected to the ATMEGA board. The “i2c-test” code was used to send values for the throttle and servo angle. When this was tested the motor and servo responded as expected.
*** Power Supply Testing Results

Once the power supply was assembled, the first test was a load test to ensure that the power supply was capable of providing 3A at 5v with an input voltage of 7.4v (the lowest anticipated battery voltage). The ripple on the output of the power supply was also measured during load testing to ensure that it was less than 200 mV under all load conditions. Then the power monitoring circuit was connected to the Raspberry Pi over I2C and tested for functionality and accuracy.

   #+caption: Results of load testing, showing 3.4A current output at 5v with 7.4v input voltage
   #+attr_html: :width 300px
   #+attr_latex: :width \linewidth/2
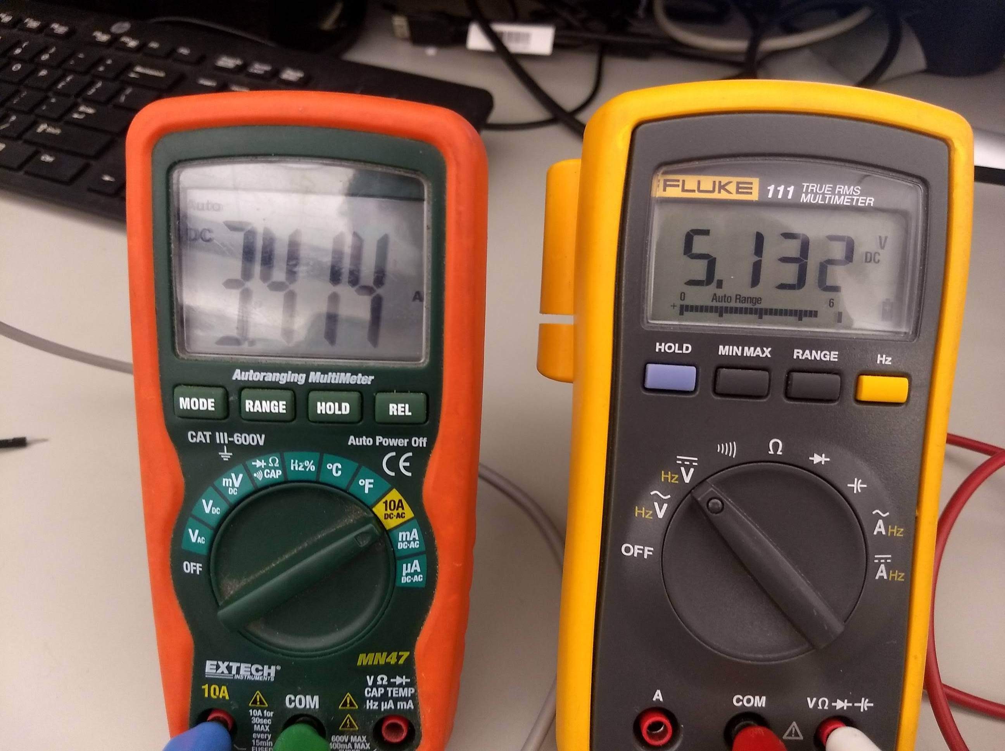
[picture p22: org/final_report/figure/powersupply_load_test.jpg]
   

   #+caption: Results of ripple testing with a 3A load and 7.4v input voltage
   #+attr_html: :width 300px
   #+attr_latex: :width \linewidth/2
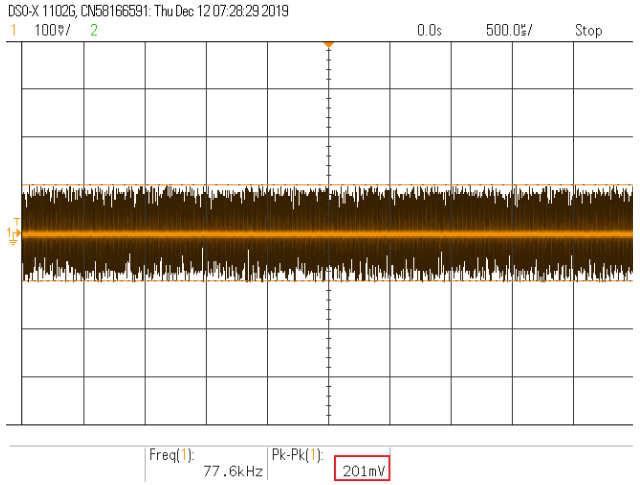
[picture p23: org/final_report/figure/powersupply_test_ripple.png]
   

For the load test, the power supply was connected to a bench power supply (set to 7.4v) and the output terminals were connected to a load resistor. The voltage and current were measured at both the input and output. An oscilloscope probe, set to AC coupling was also connected to the output to measure ripple. The maximum current delivered by the power supply was 3.4A while maintaining a 5v output. Any higher current would trigger the overcurrent protection mode on the power supply. The ripple with a 3A load was measured to be 201 mV.
   #+caption: Results of running “sensors” command, showing the voltage, current and power measurements from the power supply
   #+attr_html: :width 300px
   #+attr_latex: :width \linewidth/2
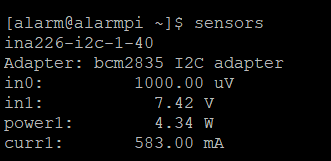
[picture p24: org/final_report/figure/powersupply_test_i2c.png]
   

The next phase of power supply testing was to ensure that the current and power monitoring section was functional. The power supply’s I2C lines were connected to the Raspberry Pi through a level converter, and the Linux driver for the power monitoring chip was loaded. The Linux utility “sensors” was used to display the measurements. The measurements were verified with a multimeter and were within 0.01 of the multimeter reading for both current and voltage measurements.

* Design Documentation (Appendix)
** System Hardware Schematic
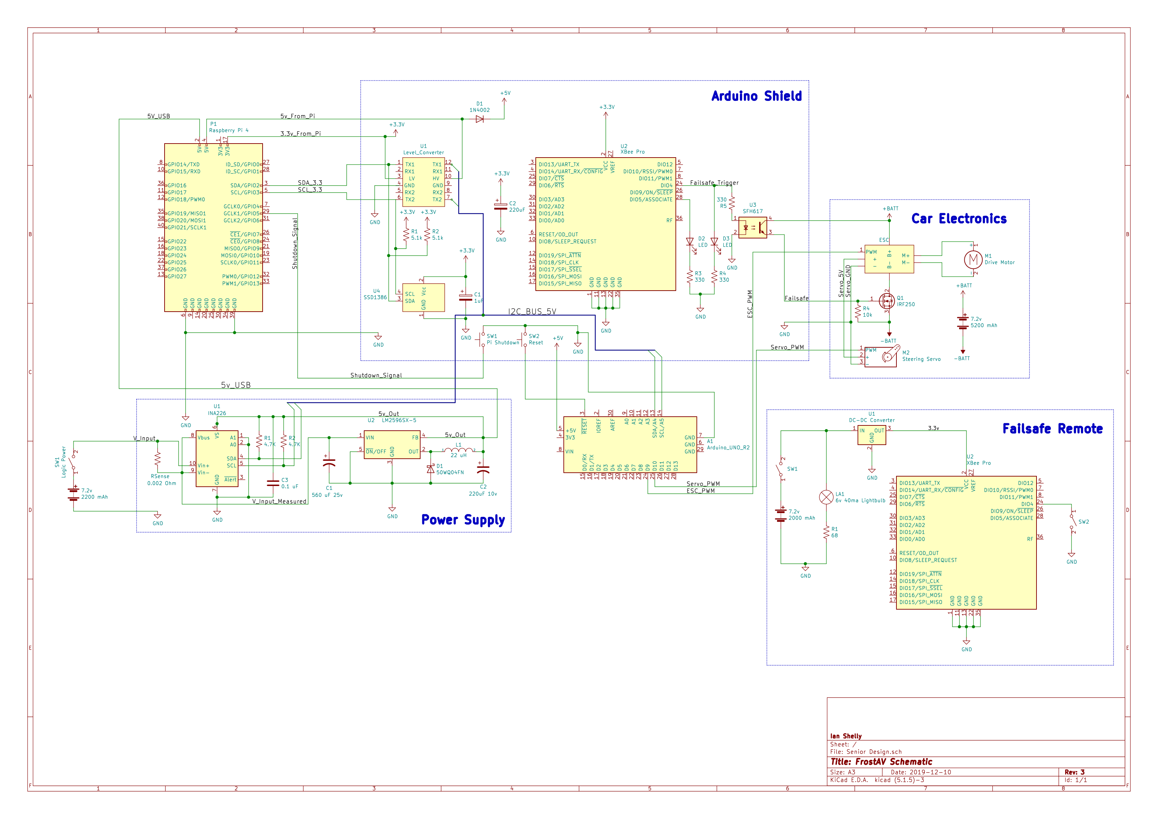
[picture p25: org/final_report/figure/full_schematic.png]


** INA226 Device Tree Overlay (ina226.dts)
#+BEGIN_SRC emacs-lisp
/dts-v1/;
/plugin/;
/ {
	fragment@0 {
		target = <&i2c1>;
		__overlay__ {
			status = "okay";
			ina226@40 {	
				compatible = "ti,ina226";
				reg = <0x40>;
				shunt-resistor = <2000>;
			};
		};
	};
};
#+END_SRC

** Raspberry Pi Boot Configuration (/boot/config.txt)

#+BEGIN_SRC emacs-lisp
# See /boot/overlays/README for all available options

gpu_mem=64
initramfs initramfs-linux.img followkernel
dtparam=i2c1=on
dtparam=i2c_arm=on
disable_overscan=1
dtoverlay=ina226
hdmi_force_hotplug=1 
dtoverlay=gpio-shutdown,gpio_pin=5
#+END_SRC

** ATMEGEA Vehicle Interface Controller
*** full.cpp
#+BEGIN_SRC emacs-lisp
#include <avr/io.h>
#include "String.hpp"
#include "usart.hpp"
#include <stdint.h>
#include "car.hpp"
#include <stdlib.h>
#include <string.h>
#include <ctype.h>
#include "usart.hpp"
#include "twi.hpp"
#include <avr/interrupt.h>

constexpr uint16_t bufferCapacity = 10;
constexpr Bounds<uint16_t> steeringAngleBounds = {50, 130};
Clamp steeringClamper = Clamp<uint16_t>::makeFromBounds(steeringAngleBounds);

void handler(uint8_t* rxbuffer, int twi_txBufferIndex);

void stateChange(String<bufferCapacity> state) {
    if (state == "+stop")
        car::stop();
}

int main() {
	twi_init();
	twi_attachSlaveRxEvent(handler);
	twi_setAddress(0x32);

    usart::beginAtBaud(9600);
    usart::print("RUNNING");
    car::start();
    
    sei();
 
	while(1) {}
}

void handler(uint8_t* rxbuffer, int twi_txBufferIndex) {
    char* message = reinterpret_cast<char*>(rxbuffer);
    //usart::print(message);
    if (message[0] == '+') stateChange(message);
    else if (isdigit(message[0])) {
        uint16_t steeringAngle = atoi(message);
        uint16_t micros = steeringClamper.mirrorMapValueToBounds(steeringAngle, car::servo::microsBounds);
        
        char steeringMessage[10];
        itoa(micros, steeringMessage, 10);
        usart::print(message);
        usart::print(", ");
        usart::print(steeringMessage);
        usart::print("\n");
        car::servo::setMicros(micros);
        //car::servo::setMirroredPositionFromBounds(steeringAngle, steeringAngleBounds);
        //car::esc::setMicrosForward(car::esc::upperBoundMicros-10);
    }
}

#+END_SRC

*** twi.cpp
#+BEGIN_SRC emacs-lisp
#include <math.h>
#include <stdlib.h>
#include <inttypes.h>
#include <avr/io.h>
#include <avr/interrupt.h>
#include <compat/twi.h>

#ifndef cbi
#define cbi(sfr, bit) (_SFR_BYTE(sfr) &= ~_BV(bit))
#endif

#ifndef sbi
#define sbi(sfr, bit) (_SFR_BYTE(sfr) |= _BV(bit))
#endif

#include "twi.hpp"

static volatile uint8_t twi_state;
static volatile uint8_t twi_slarw;
static volatile uint8_t twi_sendStop;			// should the transaction end with a stop
static volatile uint8_t twi_inRepStart;			// in the middle of a repeated start

static void (*twi_onSlaveTransmit)(void);
static void (*twi_onSlaveReceive)(uint8_t*, int);

static uint8_t twi_masterBuffer[TWI_BUFFER_LENGTH];
static volatile uint8_t twi_masterBufferIndex;
static volatile uint8_t twi_masterBufferLength;

static uint8_t twi_txBuffer[TWI_BUFFER_LENGTH];
static volatile uint8_t twi_txBufferIndex;
static volatile uint8_t twi_txBufferLength;

static uint8_t twi_rxBuffer[TWI_BUFFER_LENGTH];
static volatile uint8_t twi_rxBufferIndex;

static volatile uint8_t twi_error;

/* 
 * Function twi_init
 * Desc     readys twi pins and sets twi bitrate
 * Input    none
 * Output   none
 */
void twi_init(void)
{
  // initialize state
  twi_state = TWI_READY;
  twi_sendStop = true;		// default value
  twi_inRepStart = false;
  
  // activate internal pullups for twi.
  //digitalWrite(SDA, 1);
  //digitalWrite(SCL, 1);

  // initialize twi prescaler and bit rate
  cbi(TWSR, TWPS0);
  cbi(TWSR, TWPS1);
  TWBR = ((F_CPU / TWI_FREQ) - 16) / 2;

  /* twi bit rate formula from atmega128 manual pg 204
  SCL Frequency = CPU Clock Frequency / (16 + (2 * TWBR))
  note: TWBR should be 10 or higher for master mode
  It is 72 for a 16mhz Wiring board with 100kHz TWI */

  // enable twi module, acks, and twi interrupt
  TWCR = _BV(TWEN) | _BV(TWIE) | _BV(TWEA);
}

/* 
 * Function twi_disable
 * Desc     disables twi pins
 * Input    none
 * Output   none
 */
void twi_disable(void)
{
  // disable twi module, acks, and twi interrupt
  TWCR &= ~(_BV(TWEN) | _BV(TWIE) | _BV(TWEA));

  // deactivate internal pullups for twi.
  //digitalWrite(SDA, 0);
  //digitalWrite(SCL, 0);
}

/* 
 * Function twi_slaveInit
 * Desc     sets slave address and enables interrupt
 * Input    none
 * Output   none
 */
void twi_setAddress(uint8_t address)
{
  // set twi slave address (skip over TWGCE bit)
  TWAR = address << 1;
}

/* 
 * Function twi_setClock
 * Desc     sets twi bit rate
 * Input    Clock Frequency
 * Output   none
 */
void twi_setFrequency(uint32_t frequency)
{
  TWBR = ((F_CPU / frequency) - 16) / 2;
  
  /* twi bit rate formula from atmega128 manual pg 204
  SCL Frequency = CPU Clock Frequency / (16 + (2 * TWBR))
  note: TWBR should be 10 or higher for master mode
  It is 72 for a 16mhz Wiring board with 100kHz TWI */
}

/* 
 * Function twi_readFrom
 * Desc     attempts to become twi bus master and read a
 *          series of bytes from a device on the bus
 * Input    address: 7bit i2c device address
 *          data: pointer to byte array
 *          length: number of bytes to read into array
 *          sendStop: Boolean indicating whether to send a stop at the end
 * Output   number of bytes read
 */
uint8_t twi_readFrom(uint8_t address, uint8_t* data, uint8_t length, uint8_t sendStop)
{
  uint8_t i;

  // ensure data will fit into buffer
  if(TWI_BUFFER_LENGTH < length){
    return 0;
  }

  // wait until twi is ready, become master receiver
  while(TWI_READY != twi_state){
    continue;
  }
  twi_state = TWI_MRX;
  twi_sendStop = sendStop;
  // reset error state (0xFF.. no error occured)
  twi_error = 0xFF;

  // initialize buffer iteration vars
  twi_masterBufferIndex = 0;
  twi_masterBufferLength = length-1;  // This is not intuitive, read on...
  // On receive, the previously configured ACK/NACK setting is transmitted in
  // response to the received byte before the interrupt is signalled. 
  // Therefor we must actually set NACK when the _next_ to last byte is
  // received, causing that NACK to be sent in response to receiving the last
  // expected byte of data.

  // build sla+w, slave device address + w bit
  twi_slarw = TW_READ;
  twi_slarw |= address << 1;

  if (true == twi_inRepStart) {
    // if we're in the repeated start state, then we've already sent the start,
    // (@@@ we hope), and the TWI statemachine is just waiting for the address byte.
    // We need to remove ourselves from the repeated start state before we enable interrupts,
    // since the ISR is ASYNC, and we could get confused if we hit the ISR before cleaning
    // up. Also, don't enable the START interrupt. There may be one pending from the 
    // repeated start that we sent ourselves, and that would really confuse things.
    twi_inRepStart = false;			// remember, we're dealing with an ASYNC ISR
    do {
      TWDR = twi_slarw;
    } while(TWCR & _BV(TWWC));
    TWCR = _BV(TWINT) | _BV(TWEA) | _BV(TWEN) | _BV(TWIE);	// enable INTs, but not START
  }
  else
    // send start condition
    TWCR = _BV(TWEN) | _BV(TWIE) | _BV(TWEA) | _BV(TWINT) | _BV(TWSTA);

  // wait for read operation to complete
  while(TWI_MRX == twi_state){
    continue;
  }

  if (twi_masterBufferIndex < length)
    length = twi_masterBufferIndex;

  // copy twi buffer to data
  for(i = 0; i < length; ++i){
    data[i] = twi_masterBuffer[i];
  }
	
  return length;
}

/* 
 * Function twi_writeTo
 * Desc     attempts to become twi bus master and write a
 *          series of bytes to a device on the bus
 * Input    address: 7bit i2c device address
 *          data: pointer to byte array
 *          length: number of bytes in array
 *          wait: boolean indicating to wait for write or not
 *          sendStop: boolean indicating whether or not to send a stop at the end
 * Output   0 .. success
 *          1 .. length to long for buffer
 *          2 .. address send, NACK received
 *          3 .. data send, NACK received
 *          4 .. other twi error (lost bus arbitration, bus error, ..)
 */
uint8_t twi_writeTo(uint8_t address, uint8_t* data, uint8_t length, uint8_t wait, uint8_t sendStop)
{
  uint8_t i;

  // ensure data will fit into buffer
  if(TWI_BUFFER_LENGTH < length){
    return 1;
  }

  // wait until twi is ready, become master transmitter
  while(TWI_READY != twi_state){
    continue;
  }
  twi_state = TWI_MTX;
  twi_sendStop = sendStop;
  // reset error state (0xFF.. no error occured)
  twi_error = 0xFF;

  // initialize buffer iteration vars
  twi_masterBufferIndex = 0;
  twi_masterBufferLength = length;
  
  // copy data to twi buffer
  for(i = 0; i < length; ++i){
    twi_masterBuffer[i] = data[i];
  }
  
  // build sla+w, slave device address + w bit
  twi_slarw = TW_WRITE;
  twi_slarw |= address << 1;
  
  // if we're in a repeated start, then we've already sent the START
  // in the ISR. Don't do it again.
  //
  if (true == twi_inRepStart) {
    // if we're in the repeated start state, then we've already sent the start,
    // (@@@ we hope), and the TWI statemachine is just waiting for the address byte.
    // We need to remove ourselves from the repeated start state before we enable interrupts,
    // since the ISR is ASYNC, and we could get confused if we hit the ISR before cleaning
    // up. Also, don't enable the START interrupt. There may be one pending from the 
    // repeated start that we sent outselves, and that would really confuse things.
    twi_inRepStart = false;			// remember, we're dealing with an ASYNC ISR
    do {
      TWDR = twi_slarw;				
    } while(TWCR & _BV(TWWC));
    TWCR = _BV(TWINT) | _BV(TWEA) | _BV(TWEN) | _BV(TWIE);	// enable INTs, but not START
  }
  else
    // send start condition
    TWCR = _BV(TWINT) | _BV(TWEA) | _BV(TWEN) | _BV(TWIE) | _BV(TWSTA);	// enable INTs

  // wait for write operation to complete
  while(wait && (TWI_MTX == twi_state)){
    continue;
  }
  
  if (twi_error == 0xFF)
    return 0;	// success
  else if (twi_error == TW_MT_SLA_NACK)
    return 2;	// error: address send, nack received
  else if (twi_error == TW_MT_DATA_NACK)
    return 3;	// error: data send, nack received
  else
    return 4;	// other twi error
}

/* 
 * Function twi_transmit
 * Desc     fills slave tx buffer with data
 *          must be called in slave tx event callback
 * Input    data: pointer to byte array
 *          length: number of bytes in array
 * Output   1 length too long for buffer
 *          2 not slave transmitter
 *          0 ok
 */
uint8_t twi_transmit(const uint8_t* data, uint8_t length)
{
  uint8_t i;

  // ensure data will fit into buffer
  if(TWI_BUFFER_LENGTH < (twi_txBufferLength+length)){
    return 1;
  }
  
  // ensure we are currently a slave transmitter
  if(TWI_STX != twi_state){
    return 2;
  }
  
  // set length and copy data into tx buffer
  for(i = 0; i < length; ++i){
    twi_txBuffer[twi_txBufferLength+i] = data[i];
  }
  twi_txBufferLength += length;
  
  return 0;
}

/* 
 * Function twi_attachSlaveRxEvent
 * Desc     sets function called before a slave read operation
 * Input    function: callback function to use
 * Output   none
 */
void twi_attachSlaveRxEvent( void (*function)(uint8_t*, int) )
{
  twi_onSlaveReceive = function;
}

/* 
 * Function twi_attachSlaveTxEvent
 * Desc     sets function called before a slave write operation
 * Input    function: callback function to use
 * Output   none
 */
void twi_attachSlaveTxEvent( void (*function)(void) )
{
  twi_onSlaveTransmit = function;
}

/* 
 * Function twi_reply
 * Desc     sends byte or readys receive line
 * Input    ack: byte indicating to ack or to nack
 * Output   none
 */
void twi_reply(uint8_t ack)
{
  // transmit master read ready signal, with or without ack
  if(ack){
    TWCR = _BV(TWEN) | _BV(TWIE) | _BV(TWINT) | _BV(TWEA);
  }else{
	  TWCR = _BV(TWEN) | _BV(TWIE) | _BV(TWINT);
  }
}

/* 
 * Function twi_stop
 * Desc     relinquishes bus master status
 * Input    none
 * Output   none
 */
void twi_stop(void)
{
  // send stop condition
  TWCR = _BV(TWEN) | _BV(TWIE) | _BV(TWEA) | _BV(TWINT) | _BV(TWSTO);

  // wait for stop condition to be exectued on bus
  // TWINT is not set after a stop condition!
  while(TWCR & _BV(TWSTO)){
    continue;
  }

  // update twi state
  twi_state = TWI_READY;
}

/* 
 * Function twi_releaseBus
 * Desc     releases bus control
 * Input    none
 * Output   none
 */
void twi_releaseBus(void)
{
  // release bus
  TWCR = _BV(TWEN) | _BV(TWIE) | _BV(TWEA) | _BV(TWINT);

  // update twi state
  twi_state = TWI_READY;
}

ISR(TWI_vect)
{
  switch(TW_STATUS){
    // All Master
    case TW_START:     // sent start condition
    case TW_REP_START: // sent repeated start condition
      // copy device address and r/w bit to output register and ack
      TWDR = twi_slarw;
      twi_reply(1);
      break;

    // Master Transmitter
    case TW_MT_SLA_ACK:  // slave receiver acked address
    case TW_MT_DATA_ACK: // slave receiver acked data
      // if there is data to send, send it, otherwise stop 
      if(twi_masterBufferIndex < twi_masterBufferLength){
        // copy data to output register and ack
        TWDR = twi_masterBuffer[twi_masterBufferIndex++];
        twi_reply(1);
      }else{
	if (twi_sendStop)
          twi_stop();
	else {
	  twi_inRepStart = true;	// we're gonna send the START
	  // don't enable the interrupt. We'll generate the start, but we 
	  // avoid handling the interrupt until we're in the next transaction,
	  // at the point where we would normally issue the start.
	  TWCR = _BV(TWINT) | _BV(TWSTA)| _BV(TWEN) ;
	  twi_state = TWI_READY;
	}
      }
      break;
    case TW_MT_SLA_NACK:  // address sent, nack received
      twi_error = TW_MT_SLA_NACK;
      twi_stop();
      break;
    case TW_MT_DATA_NACK: // data sent, nack received
      twi_error = TW_MT_DATA_NACK;
      twi_stop();
      break;
    case TW_MT_ARB_LOST: // lost bus arbitration
      twi_error = TW_MT_ARB_LOST;
      twi_releaseBus();
      break;

    // Master Receiver
    case TW_MR_DATA_ACK: // data received, ack sent
      // put byte into buffer
      twi_masterBuffer[twi_masterBufferIndex++] = TWDR;
    case TW_MR_SLA_ACK:  // address sent, ack received
      // ack if more bytes are expected, otherwise nack
      if(twi_masterBufferIndex < twi_masterBufferLength){
        twi_reply(1);
      }else{
        twi_reply(0);
      }
      break;
    case TW_MR_DATA_NACK: // data received, nack sent
      // put final byte into buffer
      twi_masterBuffer[twi_masterBufferIndex++] = TWDR;
	if (twi_sendStop)
          twi_stop();
	else {
	  twi_inRepStart = true;	// we're gonna send the START
	  // don't enable the interrupt. We'll generate the start, but we 
	  // avoid handling the interrupt until we're in the next transaction,
	  // at the point where we would normally issue the start.
	  TWCR = _BV(TWINT) | _BV(TWSTA)| _BV(TWEN) ;
	  twi_state = TWI_READY;
	}    
	break;
    case TW_MR_SLA_NACK: // address sent, nack received
      twi_stop();
      break;
    // TW_MR_ARB_LOST handled by TW_MT_ARB_LOST case

    // Slave Receiver
    case TW_SR_SLA_ACK:   // addressed, returned ack
    case TW_SR_GCALL_ACK: // addressed generally, returned ack
    case TW_SR_ARB_LOST_SLA_ACK:   // lost arbitration, returned ack
    case TW_SR_ARB_LOST_GCALL_ACK: // lost arbitration, returned ack
      // enter slave receiver mode
      twi_state = TWI_SRX;
      // indicate that rx buffer can be overwritten and ack
      twi_rxBufferIndex = 0;
      twi_reply(1);
      break;
    case TW_SR_DATA_ACK:       // data received, returned ack
    case TW_SR_GCALL_DATA_ACK: // data received generally, returned ack
      // if there is still room in the rx buffer
      if(twi_rxBufferIndex < TWI_BUFFER_LENGTH){
        // put byte in buffer and ack
        twi_rxBuffer[twi_rxBufferIndex++] = TWDR;
        twi_reply(1);
      }else{
        // otherwise nack
        twi_reply(0);
      }
      break;
    case TW_SR_STOP: // stop or repeated start condition received
      // ack future responses and leave slave receiver state
      twi_releaseBus();
      // put a null char after data if there's room
      if(twi_rxBufferIndex < TWI_BUFFER_LENGTH){
        twi_rxBuffer[twi_rxBufferIndex] = '\0';
      }
      // callback to user defined callback
      twi_onSlaveReceive(twi_rxBuffer, twi_rxBufferIndex);
      // since we submit rx buffer to "wire" library, we can reset it
      twi_rxBufferIndex = 0;
      break;
    case TW_SR_DATA_NACK:       // data received, returned nack
    case TW_SR_GCALL_DATA_NACK: // data received generally, returned nack
      // nack back at master
      twi_reply(0);
      break;
    
    // Slave Transmitter
    case TW_ST_SLA_ACK:          // addressed, returned ack
    case TW_ST_ARB_LOST_SLA_ACK: // arbitration lost, returned ack
      // enter slave transmitter mode
      twi_state = TWI_STX;
      // ready the tx buffer index for iteration
      twi_txBufferIndex = 0;
      // set tx buffer length to be zero, to verify if user changes it
      twi_txBufferLength = 0;
      // request for txBuffer to be filled and length to be set
      // note: user must call twi_transmit(bytes, length) to do this
      twi_onSlaveTransmit();
      // if they didn't change buffer & length, initialize it
      if(0 == twi_txBufferLength){
        twi_txBufferLength = 1;
        twi_txBuffer[0] = 0x00;
      }
      // transmit first byte from buffer, fall
    case TW_ST_DATA_ACK: // byte sent, ack returned
      // copy data to output register
      TWDR = twi_txBuffer[twi_txBufferIndex++];
      // if there is more to send, ack, otherwise nack
      if(twi_txBufferIndex < twi_txBufferLength){
        twi_reply(1);
      }else{
        twi_reply(0);
      }
      break;
    case TW_ST_DATA_NACK: // received nack, we are done 
    case TW_ST_LAST_DATA: // received ack, but we are done already!
      // ack future responses
      twi_reply(1);
      // leave slave receiver state
      twi_state = TWI_READY;
      break;

    // All
    case TW_NO_INFO:   // no state information
      break;
    case TW_BUS_ERROR: // bus error, illegal stop/start
      twi_error = TW_BUS_ERROR;
      twi_stop();
      break;
  }
}

#+END_SRC

*** twi.hpp
#+BEGIN_SRC emacs-lisp
#ifndef twi_h
#define twi_h

  #include <inttypes.h>

  //#define ATMEGA8

  #ifndef TWI_FREQ
  #define TWI_FREQ 100000L
  #endif

  #ifndef TWI_BUFFER_LENGTH
  #define TWI_BUFFER_LENGTH 32
  #endif

  #define TWI_READY 0
  #define TWI_MRX   1
  #define TWI_MTX   2
  #define TWI_SRX   3
  #define TWI_STX   4
  
  void twi_init(void);
  void twi_disable(void);
  void twi_setAddress(uint8_t);
  void twi_setFrequency(uint32_t);
  uint8_t twi_readFrom(uint8_t, uint8_t*, uint8_t, uint8_t);
  uint8_t twi_writeTo(uint8_t, uint8_t*, uint8_t, uint8_t, uint8_t);
  uint8_t twi_transmit(const uint8_t*, uint8_t);
  void twi_attachSlaveRxEvent( void (*)(uint8_t*, int) );
  void twi_attachSlaveTxEvent( void (*)(void) );
  void twi_reply(uint8_t);
  void twi_stop(void);
  void twi_releaseBus(void);

#endif
#+END_SRC

*** car.hpp
#+BEGIN_SRC emacs-lisp
#ifndef CAR_HPP
#define CAR_HPP

#include "Clamp.hpp"
#include "dual_servo.hpp"
#include <util/delay.h>

//Arduino Uno Pins: 9 (ESC), 10 (Servo)

namespace car::servo {
    constexpr uint16_t rightBoundMicros = 1150;
    constexpr uint16_t leftBoundMicros = 1850;
    constexpr uint16_t centerMicros = 1500;
    constexpr Bounds<uint16_t> microsBounds = {
        .lower = rightBoundMicros,
        .upper = leftBoundMicros};

    uint16_t currentMicros;     
    
    namespace {
        Clamp clamper = Clamp<uint16_t>::makeFromBounds(microsBounds);
    }
    
    void setMicros(uint16_t micros) {
        dual_servo::setMicrosB(currentMicros = clamper.clamp(micros));
    }

    void setPositionFromBounds(uint16_t position, Bounds<uint16_t> bounds) {
        Clamp positionClamper = Clamp<uint16_t>::makeFromBounds(bounds);
        uint16_t micros = positionClamper.mapValueToBounds(position, microsBounds);
        setMicros(micros);
    }

    void setMirroredPositionFromBounds(uint16_t position, Bounds<uint16_t> bounds) {
        Clamp positionClamper = Clamp<uint16_t>::makeFromBounds(bounds);
        uint16_t micros = positionClamper.mirrorMapValueToBounds(position, microsBounds);
        setMicros(micros);
    }
    
    void center() {
        dual_servo::setMicrosB(currentMicros = centerMicros);
    }

    void increment(uint16_t increment) {
        setMicros(currentMicros += increment);
    }

    bool isAtLeftBound() { return currentMicros == microsBounds.upper; }
    bool isAtRightBound() { return currentMicros == microsBounds.lower; }
    bool isCentered() { return currentMicros == centerMicros; }
}

namespace car::esc {
    constexpr uint16_t upperBoundMicros = 1600;
    constexpr uint16_t lowerBoundMicros = 1420;
    constexpr uint16_t centerMicros = 1500;
    constexpr Bounds<uint16_t> forwardMicrosBounds = {
        .lower = centerMicros,
        .upper = upperBoundMicros};
    constexpr Bounds<uint16_t> reverseMicrosBounds = {
        .lower = lowerBoundMicros,
        .upper = centerMicros};

    uint16_t currentMicros; 
    
    namespace {
        Clamp forwardClamper = Clamp<uint16_t>::makeFromBounds(forwardMicrosBounds);
        Clamp reverseClamper = Clamp<uint16_t>::makeFromBounds(reverseMicrosBounds);

        void setMicrosToArm() {
            dual_servo::setMicrosA(currentMicros = centerMicros);
        }
    }
    
    void setMicrosForward(uint16_t micros) {
        dual_servo::setMicrosA(currentMicros = forwardClamper.clamp(micros));
    }
    
    void setMicrosReverse(uint16_t micros) {
        dual_servo::setMicrosA(currentMicros = reverseClamper.clamp(micros));
    }

    void arm() {
        setMicrosToArm();
        _delay_ms(2000);
    }

    void brake() {
        dual_servo::setMicrosA(currentMicros = lowerBoundMicros);
        _delay_ms(1000);
        dual_servo::setMicrosA(currentMicros = centerMicros);
    }

    void increment(uint16_t increment) {
        currentMicros += increment;
        setMicrosForward(currentMicros);
    }

    bool isAtUpperBound() { return currentMicros == forwardMicrosBounds.upper; }
    bool isAtLowerBound() { return currentMicros == reverseMicrosBounds.lower; }
    bool isCentered() { return currentMicros == centerMicros; }
}

namespace car {
    void start() {
        dual_servo::start();
        car::servo::center();
        car::esc::arm();
    }

    void stop() {
        car::servo::center();
        car::esc::brake();
    }
}

#endif

#+END_SRC

*** dualservo.hpp
#+BEGIN_SRC emacs-lisp
#ifndef DUALSERVO_HPP
#define DUALSERVO_HPP

#include <avr/io.h>
#include "cycles.hpp"

namespace dual_servo {
    void start() {
        DDRB |= 1 << PINB1; //Output from OCR1A (pin 9 Arduino Uno)
        DDRB |= 1 << PINB2; //Output from OCR1B (pin 10 Arduino Uno) 

        TCCR1A |=
            1 << WGM11 | //PWM Mode 14 (1/3)
            1 << COM1A1 | //Non-Inverting Mode
            1 << COM1B1; //Non-Inverting Mode
    
        TCCR1B |=
            1 << WGM12 | //PWM Mode 14 (2/3)
            1 << WGM13 | //PWM Mode 14 (3/3)
            1 << CS11; //Prescaler: 8

        cycles::prescaler = 8;
        ICR1 = cycles::fromHertz(50)-1;
    }

    void setMicrosA(uint16_t micros) {    
        OCR1A = cycles::fromMicros(micros);
    }

    void setMicrosB(uint16_t micros) {
        OCR1B = cycles::fromMicros(micros);
    }
}

#endif

#+END_SRC

*** Clamp.hpp
#+BEGIN_SRC emacs-lisp
#ifndef CLAMP_HPP
#define CLAMP_HPP

#include <stdint.h>

template<typename T>
struct Bounds {
    T lower;
    T upper;
};

template<typename T>
class Clamp {
    Bounds<T> bounds;

public:
    constexpr static Clamp<T> makeFromBounds(Bounds<T> bounds) {
        return Clamp(bounds);
    }

    constexpr explicit Clamp(Bounds<T> bounds): bounds{bounds} {}

    T clamp(T value) {
        return (value < bounds.lower) ? bounds.lower :
            (value > bounds.upper) ? bounds.upper:
            value;
    }
    
    T mapValueToBounds(T value, Bounds<T> other) {
        T otherRange = other.upper - other.lower;
        T thisRange = bounds.upper - bounds.lower;
        
        return other.lower + otherRange*(clamp(value) - bounds.lower)/thisRange;
    }

    T mirrorMapValueToBounds(T value, Bounds<T> other) {
        T mirroredValue = bounds.upper-value + bounds.lower;
        return mapValueToBounds(mirroredValue, other);
    }
    
    Clamp() {}
};

#endif

#+END_SRC

*** cycles.hpp
#+BEGIN_SRC emacs-lisp
#ifndef CYCLES_HPP
#define CYCLES_HPP

namespace cycles {
    constexpr uint32_t clockFrequency = F_CPU;
    static uint8_t prescaler;

    uint32_t fromMicros(uint16_t micros) {
        constexpr uint32_t unitConversion = 1E6;
        return (clockFrequency/unitConversion/prescaler) * micros;
    }

    uint32_t fromHertz(uint16_t hertz) {
        return clockFrequency/prescaler/hertz;
    }    
}

#endif

#+END_SRC

*** Makefile
#+BEGIN_SRC emacs-lisp
subdirs = $(shell find app -mindepth 1 -maxdepth 1 -type d)
all:
	make -C common
	for dir in $(subdirs); do make -C $$dir || exit 1; done

clean:
	make -C common $@
	for dir in $(subdirs); do make -C $$dir $@; done

test:
	make -C common $@

#+END_SRC

** OpenCV Lane Detection (Raspberry Pi)
*** video.py
#+BEGIN_SRC emacs-lisp
import numpy
import cv2
import math
import sys

def detect_edges(frame):
    hsv = cv2.cvtColor(frame, cv2.COLOR_BGR2HSV)
    lower_blue = numpy.array([60, 40, 40])
    upper_blue = numpy.array([150, 255, 255])
    mask = cv2.inRange(hsv, lower_blue, upper_blue)
    edges = cv2.Canny(mask, 200, 400)
    return edges
def display_lines(frame, lines, line_color=(0, 255, 0), line_width=2):
    line_image = numpy.zeros_like(frame)
    if lines is not None:
        for line in lines:
            for x1, y1, x2, y2 in line:
                cv2.line(line_image, (x1, y1), (x2, y2), line_color, line_width)
    line_image = cv2.addWeighted(frame, 0.8, line_image, 1, 1)
    return line_image
def region_of_interest(edges):
    height, width = edges.shape
    mask = numpy.zeros_like(edges)

    # only focus bottom half of the screen
    polygon = numpy.array([[
        (0, height * 1 / 2),
        (width, height * 1 / 2),
        (width, height),
        (0, height),
    ]], numpy.int32)

    cv2.fillPoly(mask, polygon, 255)
    cropped_edges = cv2.bitwise_and(edges, mask)
    return cropped_edges
def detect_line_segments(cropped_edges):
    # tuning min_threshold, minLineLength, maxLineGap is a trial and error process by hand
    rho = 1  # distance precision in pixel, i.e. 1 pixel
    angle = numpy.pi / 180  # angular precision in radian, i.e. 1 degree
    min_threshold = 10  # minimal of votes
    line_segments = cv2.HoughLinesP(cropped_edges, rho, angle, min_threshold, 
                                    numpy.array([]), minLineLength=8, maxLineGap=4)

    return line_segments
def make_points(frame, line):
    height, width, _ = frame.shape
    slope, intercept = line
    y1 = height  # bottom of the frame
    y2 = int(y1 * 1 / 2)  # make points from middle of the frame down

    # bound the coordinates within the frame
    x1 = max(-width, min(2 * width, int((y1 - intercept) / slope)))
    x2 = max(-width, min(2 * width, int((y2 - intercept) / slope)))
    return [[x1, y1, x2, y2]]

def average_slope_intercept(frame, line_segments):
    """
    This function combines line segments into one or two lane lines
    If all line slopes are < 0: then we only have detected left lane
    If all line slopes are > 0: then we only have detected right lane
    """
    lane_lines = []
    if line_segments is None:
        return lane_lines

    height, width, _ = frame.shape
    left_fit = []
    right_fit = []

    boundary = 1/3
    left_region_boundary = width * (1 - boundary)  # left lane line segment should be on left 2/3 of the screen
    right_region_boundary = width * boundary # right lane line segment should be on left 2/3 of the screen

    for line_segment in line_segments:
        for x1, y1, x2, y2 in line_segment:
            if x1 == x2:
                continue
            fit = numpy.polyfit((x1, x2), (y1, y2), 1)
            slope = fit[0]
            intercept = fit[1]
            if slope < 0:
                if x1 < left_region_boundary and x2 < left_region_boundary:
                    left_fit.append((slope, intercept))
            else:
                if x1 > right_region_boundary and x2 > right_region_boundary:
                    right_fit.append((slope, intercept))

    left_fit_average = numpy.average(left_fit, axis=0)
    if len(left_fit) > 0:
        lane_lines.append(make_points(frame, left_fit_average))

    right_fit_average = numpy.average(right_fit, axis=0)
    if len(right_fit) > 0:
        lane_lines.append(make_points(frame, right_fit_average))

    return lane_lines
def detect_lane(frame):

    edges = detect_edges(frame)
    cropped_edges = region_of_interest(edges)
    line_segments = detect_line_segments(cropped_edges)
    lane_lines = average_slope_intercept(frame, line_segments)
    
    return lane_lines
def display_heading_line(frame, steering_angle, line_color=(0, 0, 255), line_width=5 ):
    heading_image = numpy.zeros_like(frame)
    height, width, _ = frame.shape

    # figure out the heading line from steering angle
    # heading line (x1,y1) is always center bottom of the screen
    # (x2, y2) requires a bit of trigonometry

    steering_angle_radian = steering_angle / 180.0 * math.pi
    x1 = int(width / 2)
    y1 = height
    x2 = int(x1 - height / 2 / math.tan(steering_angle_radian))
    y2 = int(height / 2)
    
    cv2.putText(frame, f"{steering_angle} deg", (int(width/2) - 40, y2-10), cv2.FONT_HERSHEY_SIMPLEX, 1, (0, 0, 0), 1, cv2.LINE_AA)
    cv2.line(heading_image, (x1, y1), (x2, y2), line_color, line_width)
    heading_image = cv2.addWeighted(frame, 0.8, heading_image, 1, 1)

    return heading_image
def stabilize_steering_angle(
          curr_steering_angle, 
          new_steering_angle, 
          num_of_lane_lines, 
          max_angle_deviation_two_lines=5, 
          max_angle_deviation_one_lane=1):
    """
    Using last steering angle to stabilize the steering angle
    if new angle is too different from current angle, 
    only turn by max_angle_deviation degrees
    """
    if num_of_lane_lines == 2 :
        # if both lane lines detected, then we can deviate more
        max_angle_deviation = max_angle_deviation_two_lines
    else :
        # if only one lane detected, don't deviate too much
        max_angle_deviation = max_angle_deviation_one_lane
    
    angle_deviation = new_steering_angle - curr_steering_angle
    if abs(angle_deviation) > max_angle_deviation:
        stabilized_steering_angle = int(curr_steering_angle
            + max_angle_deviation * angle_deviation / abs(angle_deviation))
    else:
        stabilized_steering_angle = new_steering_angle
    return stabilized_steering_angle

def getMp4Colorless(name: str, fps: int) -> cv2.VideoWriter:
    return cv2.VideoWriter(
        filename = f"{name}_{fps}fps.mp4",
        fourcc = cv2.VideoWriter_fourcc(*'X264'),
        fps = fps,
        frameSize = (640,480), 
        isColor = False)

def getMp4Color(name: str, fps: int) -> cv2.VideoWriter:
    return cv2.VideoWriter(
        filename = f"{name}_{fps}fps.mp4",
        fourcc = cv2.VideoWriter_fourcc(*'X264'),
        fps = fps,
        frameSize = (640,480), 
        isColor = True)

frame = cv2.imread(sys.argv[1])
lane_lines = detect_lane(frame)
height, width, _ = frame.shape

#2 lane detected
_, _, left_x2, _ = lane_lines[0][0]
_, _, right_x2, _ = lane_lines[1][0]
mid = int(width / 2)
x_offset = (left_x2 + right_x2) / 2 - mid
y_offset = int(height / 2)

#Only 1 lane detected
# x1, _, x2, _ = lane_lines[0][0]
# x_offset = x2 - x1
# y_offset = int(height / 2)

angle_to_mid_radian = math.atan(x_offset / y_offset)  # angle (in radian) to center vertical line
angle_to_mid_deg = int(angle_to_mid_radian * 180.0 / math.pi)  # angle (in degrees) to center vertical line
steering_angle = angle_to_mid_deg + 90  # this is the steering angle needed by picar front wheel

lane_lines_image = display_lines(frame, lane_lines)
cv2.imshow("lane lines", lane_lines_image)
cv2.imshow("", display_heading_line(frame, steering_angle))
cv2.waitKey(0)

#+END_SRC

** Web Status Page
*** index.html
#+BEGIN_SRC emacs-lisp
<!DOCTYPE HTML><html>

<head>
  <meta name="viewport" content="width=device-width, initial-scale=1">
  <script src="/highcharts.js"></script>
  <title>Pi Status</title>
  <link rel="icon" href="/favicon.jpg">
  <style>
    body {
      min-width: 310px;
    	max-width: 800px;
    	height: 400px;
      margin: 0 auto;
    }
    h2 {
      font-family: Arial;
      font-size: 2.5rem;
      text-align: center;
    }
  </style>
</head>
<body>
  <h2>Vehicle Data</h2>

</form>
  <h3>Pi Data</h3>

  <h3>Power Supply Data</h3>

</body>
<script>
var chartC = new Highcharts.Chart({
  chart:{ renderTo : 'chart-temperature' },
  title: { text: 'Temperature' },
  series: [{
    name: 'CPU',
    showInLegend: true,
    data: [],
    color: '#eb5b34'
  }, {
    name: 'GPU',
    showInLegend: true,
    data: [],
    color: '#24f00a'
  }],
  plotOptions: {
    line: { animation: false,
      dataLabels: { enabled: true }
    },
    series: { color: '#059e8a' }
  },
  xAxis: { type: 'datetime',
    dateTimeLabelFormats: { second: '%H:%M:%S' }
  },
  yAxis: {
    title: { text: 'Temperature (C)' }
  },
  credits: { enabled: false }
});
setInterval(function ( ) {
  var xhttp = new XMLHttpRequest();
  xhttp.onreadystatechange = function() {
    if (this.readyState == 4 && this.status == 200) {
      var x = (new Date()).getTime(),
          y = parseFloat(this.responseText);
      //console.log(this.responseText);
      if(chartC.series[0].data.length > 40) {
        chartC.series[0].addPoint([x, y], true, true, true);
      } else {
        chartC.series[0].addPoint([x, y], true, false, true);
      }
    }
  };
  xhttp.open("GET", "/temperature_c.php", true);
  xhttp.send();  
  var xhttp = new XMLHttpRequest();
  xhttp.onreadystatechange = function() {
    if (this.readyState == 4 && this.status == 200) {
      var x = (new Date()).getTime(),
          y = parseFloat(this.responseText);
      //console.log(this.responseText);
      if(chartC.series[1].data.length > 40) {
        chartC.series[1].addPoint([x, y], true, true, true);
      } else {
        chartC.series[1].addPoint([x, y], true, false, true);
      }
    }
  };
  xhttp.open("GET", "/temperature_g.php", true);
  xhttp.send();

}, 1000 ) ;

var chartL = new Highcharts.Chart({
  chart:{ renderTo : 'chart-load' },
  title: { text: 'System Load' },
  series: [{
    showInLegend: false,
    data: []
  }],
  plotOptions: {
    line: { animation: false,
      dataLabels: { enabled: true }
    },
    series: { color: '#059e8a' }
  },
  xAxis: { type: 'datetime',
    dateTimeLabelFormats: { second: '%H:%M:%S' }
  },
  yAxis: {
  },
  credits: { enabled: false }
});
setInterval(function ( ) {
  var xhttp = new XMLHttpRequest();
  xhttp.onreadystatechange = function() {
    if (this.readyState == 4 && this.status == 200) {
      var x = (new Date()).getTime(),
          y = parseFloat(this.responseText);
      //console.log(this.responseText);
      if(chartL.series[0].data.length > 40) {
        chartL.series[0].addPoint([x, y], true, true, true);
      } else {
        chartL.series[0].addPoint([x, y], true, false, true);
      }
    }
  };
  xhttp.open("GET", "/load.php", true);
  xhttp.send();
}, 1000 ) ;

var chartM = new Highcharts.Chart({
  chart:{ renderTo : 'chart-mem' },
  title: { text: 'Memory' },
  series: [{
    name: 'Used Memory',
    color: '#00FF00',
    showInLegend: true,
    data: []
  }, {
  name: 'Free Memory',
  color: '#FF00FF',
  showInLegend: true,
  data: []
  }],
  plotOptions: {
    line: { animation: false,
      dataLabels: { enabled: true }
    },
    series: { color: '#059e8a' }
  },
  xAxis: { type: 'datetime',
    dateTimeLabelFormats: { second: '%H:%M:%S' }
  },
  yAxis: {
    title: {text: "Memory (Mb)" }
  },
  credits: { enabled: false }
});
setInterval(function ( ) {
  var xhttp = new XMLHttpRequest();
  xhttp.onreadystatechange = function() {
    if (this.readyState == 4 && this.status == 200) {
      var x = (new Date()).getTime(),
          y = parseFloat(this.responseText);
      if(chartM.series[0].data.length > 40) {
        chartM.series[0].addPoint([x, y], true, true, true);
      } else {
        chartM.series[0].addPoint([x, y], true, false, true);
      }
    }
  };
  xhttp.open("GET", "/memory.php", true);
  xhttp.send();
  var xhttp = new XMLHttpRequest();
  xhttp.onreadystatechange = function() {
    if (this.readyState == 4 && this.status == 200) {
      var x = (new Date()).getTime(),
          y = parseFloat(this.responseText);
      if(chartM.series[1].data.length > 40) {
        chartM.series[1].addPoint([x, y], true, true, true);
      } else {
        chartM.series[1].addPoint([x, y], true, false, true);
      }
    }
  };
  xhttp.open("GET", "/memfree.php", true);
  xhttp.send();

}, 1000 ) ;

var chartT = new Highcharts.Chart({
  chart:{ renderTo : 'chart-power' },
  title: { text: 'Power' },
  series: [{
    showInLegend: false,
    data: []
  }],
  plotOptions: {
    line: { animation: false,
      dataLabels: { enabled: true }
    },
    series: { color: '#059e8a' }
  },
  xAxis: { type: 'datetime',
    dateTimeLabelFormats: { second: '%H:%M:%S' }
  },
  yAxis: {
    title: { text: 'Power (W)' }
  },
  credits: { enabled: false }
});
setInterval(function ( ) {
  var xhttp = new XMLHttpRequest();
  xhttp.onreadystatechange = function() {
    if (this.readyState == 4 && this.status == 200) {
      var x = (new Date()).getTime(),
          y = parseFloat(this.responseText);
      //console.log(this.responseText);
      if(chartT.series[0].data.length > 40) {
        chartT.series[0].addPoint([x, y], true, true, true);
      } else {
        chartT.series[0].addPoint([x, y], true, false, true);
      }
    }
  };
  xhttp.open("GET", "/power.php", true);
  xhttp.send();
}, 1000 ) ;

var chartH = new Highcharts.Chart({
  chart:{ renderTo:'chart-voltage' },
  title: { text: 'Battery Voltage' },
  series: [{
    showInLegend: false,
    data: []
  }],
  plotOptions: {
    line: { animation: false,
      dataLabels: { enabled: true }
    }
  },
  xAxis: {
    type: 'datetime',
    dateTimeLabelFormats: { second: '%H:%M:%S' }
  },
  yAxis: {
    title: { text: 'Voltage (V)' }
  },
  credits: { enabled: false }
});
setInterval(function ( ) {
  var xhttp = new XMLHttpRequest();
  xhttp.onreadystatechange = function() {
    if (this.readyState == 4 && this.status == 200) {
      var x = (new Date()).getTime(),
          y = parseFloat(this.responseText);
      //console.log(this.responseText);
      if(chartH.series[0].data.length > 40) {
        chartH.series[0].addPoint([x, y], true, true, true);
      } else {
        chartH.series[0].addPoint([x, y], true, false, true);
      }
    }
  };
  xhttp.open("GET", "/voltage.php", true);
  xhttp.send();
}, 1000 ) ;

var chartP = new Highcharts.Chart({
  chart:{ renderTo:'chart-current' },
  title: { text: 'Battery Current' },
  series: [{
    showInLegend: false,
    data: []
  }],
  plotOptions: {
    line: { animation: false,
      dataLabels: { enabled: true }
    },
    series: { color: '#18009c' }
  },
  xAxis: {
    type: 'datetime',
    dateTimeLabelFormats: { second: '%H:%M:%S' }
  },
  yAxis: {
    title: { text: 'Current (mA)' }
  },
  credits: { enabled: false }
});
setInterval(function ( ) {
  var xhttp = new XMLHttpRequest();
  xhttp.onreadystatechange = function() {
    if (this.readyState == 4 && this.status == 200) {
      var x = (new Date()).getTime(),
          y = parseFloat(this.responseText);
      //console.log(this.responseText);
      if(chartP.series[0].data.length > 40) {
        chartP.series[0].addPoint([x, y], true, true, true);
      } else {
        chartP.series[0].addPoint([x, y], true, false, true);
      }
    }
  };
  xhttp.open("GET", "/current.php", true);
  xhttp.send();
}, 1000 ) ;
</script>
</html>
#+END_SRC

*** power.php
#+BEGIN_SRC emacs-lisp
<?php 
  
// Use ls command to shell_exec 
// function 
$output = shell_exec('(sensors | grep power)'); //'bash -c 'sensors');// | grep power | sed 's/[^0-9]*//g'''); 

$output = preg_replace('/^[^:]+:\s*/', '' ,$output); 

$output = preg_replace('/[^0-9^.]*/', '', $output); 

//$output2 = preg_replace( '[^0-9]*', '', $output); 
// Display the list of all file 
// and directory 
echo "$output"; 
?> 

#+END_SRC

*** load.php
#+BEGIN_SRC emacs-lisp
<?php 
  
// Use ls command to shell_exec 
// function 
$output = shell_exec('cat /proc/loadavg');  

$output = substr ( $output, 0, 4);

echo "$output"; 
?> 

#+END_SRC

*** temperature_c.php
#+BEGIN_SRC emacs-lisp
<?php 
  
// Use ls command to shell_exec 
// function 
$output = shell_exec('cat /sys/class/thermal/thermal_zone0/temp');  

$output = $output / 1000;

echo "$output"; 
?> 

#+END_SRC

*** temperature_g.php
#+BEGIN_SRC emacs-lisp
<?php 
  
// Use ls command to shell_exec 
// function 
$output = shell_exec('/opt/vc/bin/vcgencmd measure_temp');  

$output = preg_replace("/[^0-9]/", "",$output);

$output = $output / 10;

echo "$output"; 
?> 

#+END_SRC

*** voltage.php
#+BEGIN_SRC emacs-lisp
<?php `
  
// Use ls command to shell_exec 
// function 
$output = shell_exec('(sensors | grep in1)'); //'bash -c 'sensors');// | grep power | sed 's/[^0-9]*//g'''); 

$output = preg_replace('/^[^:]+:\s*/', '' ,$output); 

$output = preg_replace('/[^0-9^.]*/', '', $output); 

//$output2 = preg_replace( '[^0-9]*', '', $output); 
// Display the list of all file 
// and directory 
echo "$output"; 
?> 

#+END_SRC

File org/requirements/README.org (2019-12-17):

#+options: num:nil toc:nil
#+latex_header: \usepackage[letterpaper, margin = 0.8in]{geometry}
#+export_exclude_tags: noexport

#+title: FrostAV: System Requirements Specification
#+author: Lewis Collum, Ian Shelly, Justin Marcy
#+date: Updated \today

* Contents                                                         :noexport:
  :PROPERTIES:
  :TOC:      this
  :END:
  -  [[#introduction][Introduction]]
    -  [[#identification][Identification]]
    -  [[#problem-overview][Problem Overview]]
    -  [[#intended-standards][Intended Standards]]
  -  [[#system-requirements][System Requirements]]
    -  [[#problem-domain-requirements][Problem-Domain Requirements]]
    -  [[#control-requirements][Control Requirements]]
    -  [[#autonomy-requirements][Autonomy Requirements]]
    -  [[#interface-requirements][Interface Requirements]]
  -  [[#system-constraints][System Constraints]]
    -  [[#sensor-constraints][Sensor Constraints]]
    -  [[#financial-constraints][Financial Constraints]]

* Introduction
  :PROPERTIES:
  :CUSTOM_ID: introduction
  :TOC:      1
  :END:
** Identification
   This document is the System Requirements Specification (SyRS) for
   FrostAV, an autonomous vehicle project, under the supervision of
   Clarkson University's Computer Engineering department. 

** Problem Overview
   :PROPERTIES:
   :CUSTOM_ID: sec:problemOverview
   :END:
  The system to be specified requires the design and construction of
  an autonomous car that has the ability to navigate within a
  _lane_. The system should satisfy the tasks specified in section
  [[#problem-domain-requirements]]. Furthermore, the car must have
  wireless communication abilities. And, the sensor systems
  implemented on the car must be minimally invasive (see section
  [[#sensor-constraints]]).
  
# * COMMENT System Abstraction
#   :PROPERTIES:
#   :CUSTOM_ID: system-abstraction
#   :TOC:      0
#   :END:
#   Each stage of the project will rest on the following fundamental
#   diagrammatic abstraction. This abstraction satisfies the
#   requirements for a minimally invasive sensor system, and the ability
#   to network wirelessly. These requirements are discussed in section
#   [[#functional-requirements]].

#   Also, note that the design presented in figure
#   [[system-abstraction_diagram]] exists entirely on the body of the car.
  
#   #+name: system-abstraction_diagram
#   #+caption: A Networker provides a path for data or commands from the wirless bus to the wired bus and vice versa. System components on the vehicle communicate to each other via the wired bus. 
#   #+attr_latex: :width \linewidth/2  
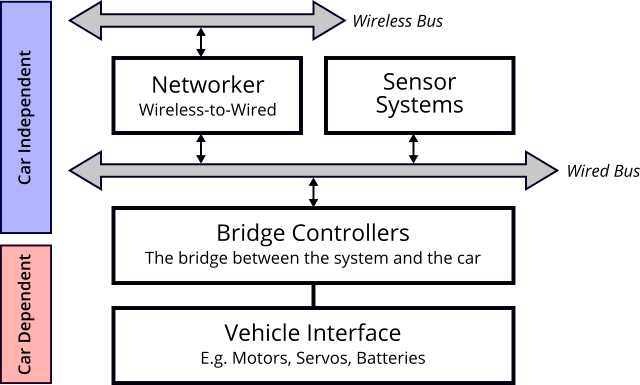
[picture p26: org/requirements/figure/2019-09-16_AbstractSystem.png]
#   

#   In reference to figure [[system-abstraction_diagram]], the
#   "car-independent" components include the Networker, Sensor Systems,
#   and the abstract portion of the Bridge Controllers; the
#   "car-dependent" components include any motors, servos, or power
#   systems for car, plus the concrete portions of the Bridge
#   Controllers.

** Intended Standards
   - ISO/IEC 29110: Systems and Software Life Cycle Profiles and Guidelines for Very Small Entities (VSEs)

* System Requirements
  :PROPERTIES:
  :CUSTOM_ID: system-requirements
  :TOC:      1
  :END:
** Problem-Domain Requirements
   :PROPERTIES:
   :CUSTOM_ID: problem-domain-requirements
   :END:
   1. Given a _lane_, the car must travel approximately parallel to it,
      such that the car stays within its _boundaries_ consistently,
      and, if the car is to accidentally leave it, it promptly
      returns.
   2. Given a _corner_, the car must turn, continuing from the car’s
      current _lane_ to the next, such that the car stays within its
      _boundaries_ consistently, and, if the car is to accidentally
      leave it, it promptly returns.
   3. Given an _obstacle_, the car must stop until it is moved
      further from the car, or it is removed from _circuit boundaries_.
   4. Given a _sign_, the car must respond to the event provided by it.
   5. Given a _circuit_, the car must complete a full loop.

   #+caption: An example _circuit_ which the car must navigate through. Provides visuals for the definitions in section [[#environmental-definitions]].
   #+attr_html: :width 300px
   #+attr_latex: :width \linewidth/2
   
   
*** Problem-Domain Definitions
    :PROPERTIES:
    :CUSTOM_ID: environmental-definitions
    :END:

    | Term             | Definition                                                              |
    |------------------+-------------------------------------------------------------------------|
    | Corner           | A sharp change in path direction that connects two lanes                |
    | Lane             | A path that has a _boundary_                                            |
    | Boundary         | The area between two parallel _edges_                                   |
    | Edge             | A line or a curve                                                       |
    | Circuit Boundary | All connected _boundaries_ which define the total area of the _circuit_ |
    | Circuit          | A closed path defined by connected _lanes_ and _corners_                |
    | Obstacle         | Any object that lies within _circuit boundaries_                        |
    | Sign             | A flat image mounted to a post outside of _circuit boundaries_          |

** Control Requirements
   :PROPERTIES:
   :CUSTOM_ID: control-requirements
   :END:
*** Control System:
    The Control System shall:
   1. Interface with vehicle peripherals, such as, motors, servos,
      batteries, etc.
   2. Be the only system coupled to the vehicle. 
   3. Have a subset of Control Modules for each peripheral in need
      of control.

*** Control Modules:
    Each Control Module shall:
   1. Encapsulate a single purpose, such that, one controller controls
      a single peripheral.
   2. Couple to a peripheral electronically, not mechanically.
   3. Be able to communicate with other controllers via a wired bus.
   4. Be able to communicate with non-controllers that depend on it,
      via a wired bus.
   5. Communicate with other controllers and non-controllers via a
      single shared wired bus.
      
** Autonomy Requirements
   The Autonomy System shall:
   1. Not be directly coupled to the Vehicle Interface (section [[#vehicle-interface-requirements]]).
   2. Be able to fit on the vehicle.
   3. Allow the vehicle to navigate, as per section
      [[#problem-domain-requirements]], without user interaction.
   4. Be able to communicate with the Control System (section [[#control-requirements]]).
** Interface Requirements
   :PROPERTIES:
   :CUSTOM_ID: interface-requirements
   :END:
*** Vehicle Interface Requirements
    :PROPERTIES:
    :CUSTOM_ID: vehicle-interface-requirements
    :END:
    The Vehicle Interface shall:
    1. Include a way for the vehicle to be turned on and off, such
       that, the vehicle receives no power to the _drive system_ or
       _logic_ when off.
    2. Include a way for the vehicle to have its _logic_ turned on,
       while the _drive system_ is off.
    3. Provide a battery peripheral that powers the _logic_.
    4. Provide a battery peripheral that powers the _drive system_.
    5. The total power consumption of the _logic_ and _drive system_
       cannot exceed the maximum capacity of the battery
       peripheral(s).
    6. Provide a peripheral that moves the vehicle.
    7. Provide a peripheral that steers the vehicle.
    8. Provide an electronic interface from each peripheral.

    | Term         | Definition                                                    |
    |--------------+---------------------------------------------------------------|
    | Logic        | Eletronic Systems including the Control and Autonomy Systems  |
    | Drive System | The electromechanical parts on the car, such as, the motor(s) |
    
*** Wireless Interface Requirements
    :PROPERTIES:
    :CUSTOM_ID: wireless-interface-requirements
    :END:
    The Wireless Interface shall:
    1. Allow for wireless tunneling (e.g. via SSH)
    2. Be able to access a server.
    3. Provide bi-directional communication.
    
* System Constraints
  :PROPERTIES:
  :CUSTOM_ID: system-constraints
  :TOC:      1
  :END:
** Sensor Constraints
   :PROPERTIES:
   :CUSTOM_ID: sensor-constraints
   :END:
   1. The sensors to go on the vehicle must be minimally invasive such
      that any sensor attached to the chassis is not coupled to an
      existing mechanism on the chassis. For example, an encoder
      cannot be used since it is coupled to the vehicle drive
      system. Sensors such as accelerometers and cameras can be used
      since they can be attached to the chassis, but are independent
      of existing vehicle mechanisms.

** Financial Constraints
   :PROPERTIES:
   :CUSTOM_ID: financial-constraints
   :TOC:      0
   :END:
   1. The FrostAV team shall not exceed $300 towards parts under the
      superivision of Clarkson University's Department of Computer
      Engineering.

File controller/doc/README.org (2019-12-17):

* Tasks
  - [5/5] *Makefile Organization* 11/19/2019
    1. [X] Build Makefile.conf including contents of current top-level Makefile.
       + Edit: split configurations into 'mk' directory .mk files (e.g. rules.mk, toolchain.mk)
    2. [X] Redo current top-level Makefile to call all subdirectory makefiles 
    3. [X] Build Makefile for 'sweep' application code
    4. [X] Figure out way to include common library among application code.
    5. [X] Test that the top-level Makefile calls 'sweep' Makefile
  - [4/4] *AVR C++ Code for Speed Controller Sweeping* 11/19/2019
    1. [X] Setup motor test with Pololu Speed Controller
       - Use RC car speed controller if this one does not work.
    2. [X] Test with Arduino that Servo library works with the speed controller.
    3. [X] Write AVR C++ register-level code for speed controller.
    4. [X] Generalize Servo and Speed Controller register-level code.
  - [X] *Multiple PWM Devices (servo, ESC) Using Same Timer* 11/20/2019
  - [X] *Use Makefile Defined FCPU Instead of Passing Clock Frequency to usart* 11/22/2019
  - [2/6] *Improve 'car' namespace with more streamline functions* 12/06/2019
    - [ ] servo should track its current micros
    - [ ] esc should track its current micros
    - [X] manual test code for servo
    - [X] manual test code for esc
    - [ ] 'brake' function for esc
    - [ ] extract class from 'car' for Bounds that track a 'current'
      variable. Include helper functions such as isAtMax().
  - [0/2] *I2C State Machine* 12/08/2019
    - [ ] check for state change which happens when the first
      character is '+' of the I2C receive buffer.
    - [ ] States
      - [ ] Brake
      - [ ] Reset
      - [ ] Start

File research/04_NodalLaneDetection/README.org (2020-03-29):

#+setupfile: ../research.org

#+title: Nodal Lane Detection
#+date: Updated: \today
#+author: Lewis Collum
*Started 03/04/2020*

* Concept
** Concept Example
   #+begin_src python :results output
class Subject:
    def __init__(self, observers: list):
        self.observers = observers

    def notifyObservers(self, data):
        for observer in self.observers:
            observer.grab(data)

class Observer:
    def grab(self, data):
        print(data)

observerA = Observer()
observerB = Observer()
subject = Subject([observerA, observerB])

subject.notifyObservers("pickle")

class Node:
    def __init__(self, strategy, observers: list):
        self.observers = observers
        self.strategy = strategy

    def notifyObservers(self, data):
        for observer in self.observers:
            observer.grab(data)
    
    def grab(self, data):
        self.notifyObservers(self.strategy(data))

nodeB = Node(
    strategy = lambda data: print(data*3),
    observers = [])

nodeA = Node(
    strategy = lambda data: data*2,
    observers = [nodeB])

head = Node(
    strategy = None,
    observers = [nodeA])

head.notifyObservers(data = 1)

def doA(data):
    return data*3

def doB(data):
    return data*2

A = doA(1)
B = doB(A)
print(B)
   #+end_src

   #+RESULTS:
   : pickle
   : pickle
   : 6
   : 6

* Application
** Sandbox
   #+begin_src python :tangle sandbox.py
import cv2
import numpy

from Node import Node
import distributor
from MaskEdgeDetector import MaskEdgeDetector
from TwoLineAverage import TwoLineAverage
from WhiteBalancer import WhiteBalancer
import segment
import frame_distributor
from displayer import Displayer, LineDisplayer
import roi
    
twoLineAverageNode = Node(
    strategy = TwoLineAverage(
        frameShape = frame_distributor.grabCaptureFrame().shape,
        insetPercentage = 0.60),
    observers = [LineDisplayer()])

edgeSegmentatorNode = Node(
    strategy = segment.EdgeSegmentator(
        distancePrecision = 1,
        angularPrecision = numpy.pi/180,
        minimumThreshold = 40),
    observers = [twoLineAverageNode])

regionOfInterestNode = Node(
    strategy = roi.RegionOfInterest(insetWeight = 0.75),
    observers = [edgeSegmentatorNode])

cannyNode = Node(lambda mask: cv2.Canny(mask, 200, 400), [edgeSegmentatorNode, Displayer()])

hsvMaskNode = Node(lambda frame: cv2.inRange(frame, numpy.asarray([100, 50, 110]), numpy.asarray([120, 255, 255])), [cannyNode])
labMaskNode = Node(lambda frame: cv2.inRange(frame, numpy.asarray([0, 0, 110]), numpy.asarray([255, 255, 255])), [cannyNode])

labNode = Node(lambda frame: cv2.cvtColor(frame, cv2.COLOR_BGR2LAB), [Displayer(), labMaskNode])
hsvNode = Node(lambda frame: cv2.cvtColor(frame, cv2.COLOR_BGR2HSV), [Displayer(), hsvMaskNode])
balancerNode = Node(WhiteBalancer(), [labNode])

frame_distributor.startAtHead([labNode])
   #+end_src
** Model
   #+begin_src python :tangle laneModel.py
import cv2
import numpy

import lane
import frame

labNode = lane.Node(
    subjects = [frame.subject],
    strategy = lambda frame: cv2.cvtColor(frame, cv2.COLOR_BGR2LAB))

labMaskNode = lane.Node(
    subjects = [labNode],
    strategy = lambda frame: cv2.inRange(frame, numpy.asarray([0, 0, 110]), numpy.asarray([255, 255, 255])))

cannyNode = lane.Node(
    subjects = [labMaskNode],
    strategy = lambda mask: cv2.Canny(mask, 200, 400))

regionOfInterestNode = lane.Node(
    subjects = [cannyNode],
    strategy = lane.RegionOfInterest(insetWeight = 0.75))

edgeSegmentatorNode = lane.Node(
    subjects = [regionOfInterestNode],
    strategy = lane.EdgeSegmentator(
        distancePrecision = 1,
        angularPrecision = numpy.pi/180,
        minimumThreshold = 40))

twoLineAverageNode = lane.Node(
    subjects = [edgeSegmentatorNode],
    strategy = lane.TwoLineAverage(
        frameShape = frame.subject.grabCaptureFrame().shape,
        insetPercentage = 0.60))
   #+end_src

* Frame
** init
   #+begin_src python :tangle frame/__init__.py
from . import subject
from .displayer import Displayer, LineDisplayer
from .line import addLines

import cv2
def toImage(frame):
    return cv2.imencode('.jpg', frame)[1].tobytes()
   #+end_src
** displayer
   #+begin_src python :tangle frame/displayer.py
import cv2
import numpy

from .line import addLines
from . import subject

class Displayer:
    def __init__(self):
        self.imageName = newImageName()
    
    def __call__(self, frame):
        cv2.imshow(f"{self.imageName}", frame)

class LineDisplayer:
    def __init__(self):
        self.imageName = newImageName()
        
    def __call__(self, lines):
        frame = addLines(lines)
        cv2.imshow(f"{self.imageName}", frame)

totalDisplayers = 0
def newImageName():
    global totalDisplayers
    name = totalDisplayers
    totalDisplayers += 1
    return name
   #+end_src
** subject
   #+begin_src python :tangle frame/subject.py
import cv2
import sys
import threading 

source = 0
observers = []
currentFrame = None

def getCurrentFrame():
    return currentFrame

def addObservers(others):
    global observers
    observers += others

def grabCaptureFrame():
    capture = cv2.VideoCapture(source)
    _, frame = capture.read()
    capture.release()
    return frame

def startCapture():
    capture = cv2.VideoCapture(source)
    while True: #cv2.waitKey(33) != ord('q'):
        hasFrame, frame = capture.read()
        print(f"SUBJECT READ: {hasFrame}")
        if hasFrame:
            global currentFrame
            currentFrame = frame
            for observer in observers: observer(currentFrame)

captureThread = None
def startThreadedCapture():
    global captureThread
    if captureThread == None:
        captureThread = threading.Thread(target=startCapture)
        captureThread.start()

def stop():
    capture.release()
    cv2.destroyAllWindows()
   #+end_src
** line
#+begin_src python :tangle frame/line.py
import cv2
import numpy

from . import subject

def addLines(lines):
    frame = subject.getCurrentFrame()
    lineFrame = numpy.zeros_like(frame)
    for line in lines:
        x1, y1, x2, y2 = line[0]
        cv2.line(lineFrame, (x1, y1), (x2, y2), (0, 255, 0), 2)
        
    lineFrame = cv2.addWeighted(frame, 0.8, lineFrame, 1, 1)    
    return lineFrame
#+end_src
* Lane Package
** init
   #+begin_src python :tangle lane/__init__.py
from .Node import Node
from .MaskEdgeDetector import MaskEdgeDetector
from .TwoLineAverage import TwoLineAverage
from .segment import EdgeSegmentator
from .roi import RegionOfInterest
   #+end_src

** Node
   #+begin_src python :tangle lane/Node.py
class Node:
    def __init__(self, subjects, strategy):
        self.strategy = strategy
        self.observers = []
        for subject in subjects: subject.addObservers([self])
        self.output = None
                
    def addObservers(self, observers):
        self.observers += observers
        
    def __call__(self, package):
        self.output = self.strategy(package)
        for observer in self.observers:
            observer(self.output)
   #+end_src

** Edge Detect
   #+begin_src python :tangle lane/MaskEdgeDetector.py
import cv2

class MaskEdgeDetector:
    def __init__(self, maskLower, maskUpper):
        self.maskLower = maskLower
        self.maskUpper = maskUpper

    def __call__(self, frame):
        mask = cv2.inRange(frame, self.maskLower, self.maskUpper)
        edges = cv2.Canny(mask, 200, 400)
        return edges

class HsvMaskEdgeDetector:
    def __init__(self, maskLower, maskUpper):
        self.maskLower = maskLower
        self.maskUpper = maskUpper

    def __call__(self, frame):
        mask = cv2.inRange(frame, self.maskLower, self.maskUpper)
        edges = cv2.Canny(mask, 200, 400)
        return edges
   #+end_src

** Hough Lines
   #+begin_src python :tangle lane/segment.py
import cv2
import numpy

class EdgeSegmentator:
    def __init__(self, distancePrecision, angularPrecision, minimumThreshold):
        self.distancePrecision = distancePrecision
        self.angularPrecision = angularPrecision
        self.minimumThreshold = minimumThreshold
        
    def __call__(self, frame):
        segments = cv2.HoughLinesP(
            frame,
            self.distancePrecision,
            self.angularPrecision,
            self.minimumThreshold,
            numpy.array([]),
            minLineLength=8,
            maxLineGap=4)
        return () if isinstance(segments, type(None)) else segments    
   #+end_src
** Region of Interest
   #+begin_src python :tangle lane/roi.py
import cv2
import numpy

class RegionOfInterest:
    def __init__(self, insetWeight = 1):
        self.insetWeight = insetWeight
        
    def __call__(self, frame):
        height, width = frame.shape
        mask = numpy.zeros_like(frame)
        
        polygon = numpy.array([[
            (width * self.insetWeight/2, 0),
            (width * (1 - self.insetWeight/2), 0),
            (width, height),
            (0, height),
        ]], numpy.int32)
        
        cv2.fillPoly(mask, polygon, 255)
        frame = cv2.bitwise_and(frame, mask)
        return frame        
   #+end_src
** White Balancer
   #+begin_src python :tangle lane/WhiteBalancer.py
class WhiteBalancer:
    def __call__(self, frame):
        balanced_img = numpy.zeros_like(frame) #Initialize final image

        for i in range(3): #i stands for the channel index 
            hist, bins = numpy.histogram(frame[..., i].ravel(), 256, (0, 256))
            bmin = numpy.min(numpy.where(hist>(hist.sum()*0.0005)))
            bmax = numpy.max(numpy.where(hist>(hist.sum()*0.0005)))
            balanced_img[...,i] = numpy.clip(frame[...,i], bmin, bmax)
            balanced_img[...,i] = (balanced_img[...,i]-bmin) / (bmax - bmin) * 255
            
        return balanced_img
   #+end_src

** Two Line Average
   #+begin_src python :tangle lane/TwoLineAverage.py
import numpy

class TwoLineAverage:
    def __init__(self, frameShape, insetPercentage):
        self.height, width, _ = frameShape
        self.leftBoundary = width * (1-insetPercentage)
        self.rightBoundary = width * insetPercentage
        
    def __call__(self, lines):
        lanes = []
        left = []
        right = []
        total = []

        for line in lines:
            x1, y1, x2, y2 = line[0].astype(int)
            top = (x1, y1) if y1 > y2 else (x2, y2)
            bottom = (x1, y1) if y1 < y2 else (x2, y2)
            dx = bottom[0] - top[0]
            dy = bottom[1] - top[1]
            topToFrameBottom = self.height - top[1]
            bottomXIntersept = topToFrameBottom/dy * dx + top[0]
            if bottomXIntersept <= self.leftBoundary:
                left.append(numpy.asarray([bottomXIntersept, *top, *bottom]))
            if bottomXIntersept >= self.rightBoundary:
                right.append(numpy.asarray([bottomXIntersept, *top, *bottom]))

        if len(left) >= 3:
            leftAverage = numpy.mean(left, axis = 0).astype(int)
            lanes.append([[leftAverage[0], self.height, leftAverage[1], leftAverage[2]]])

        if len(right) >= 3:
            rightAverage = numpy.mean(right, axis = 0).astype(int)
            lanes.append([[rightAverage[0], self.height, rightAverage[1], rightAverage[2]]])
            
        return lanes
   #+end_src
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

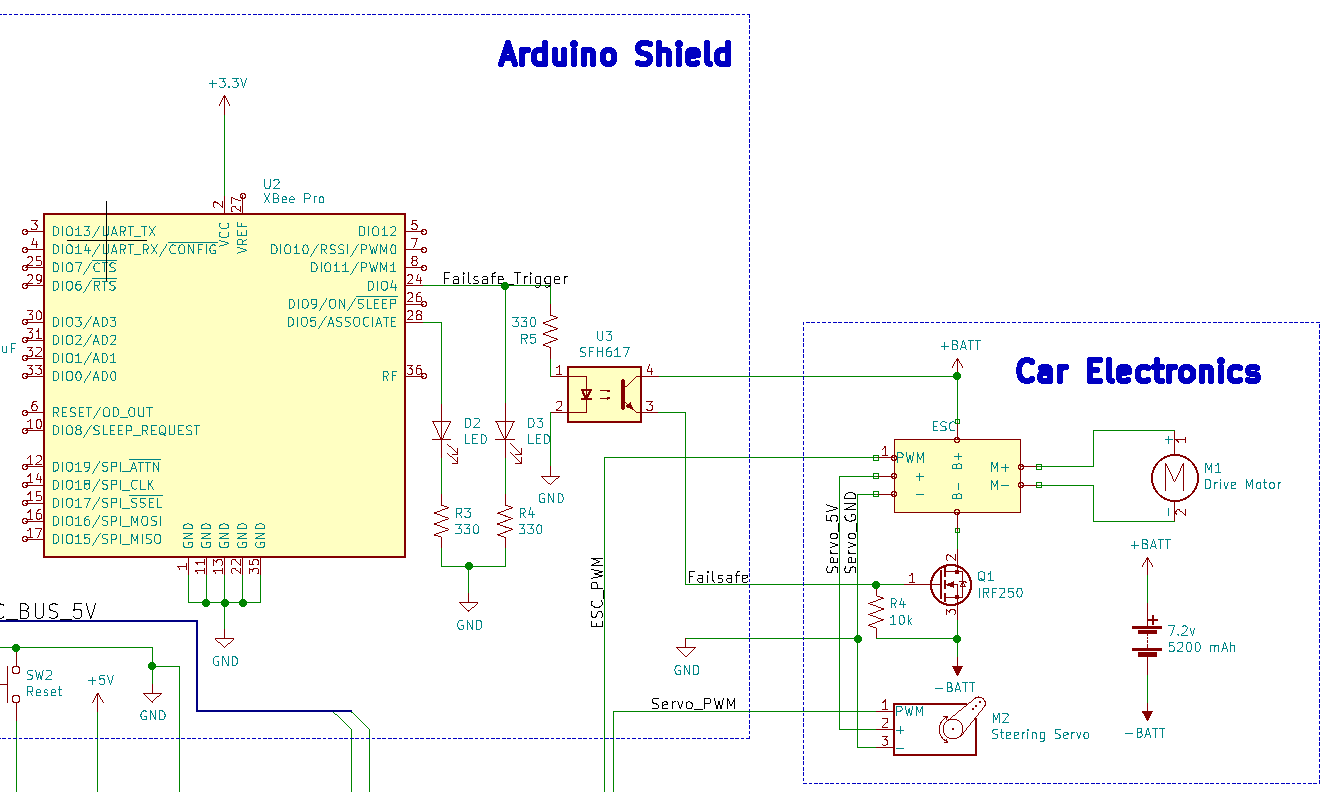
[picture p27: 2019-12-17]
org/final_report/figure/failsafe_carside.png

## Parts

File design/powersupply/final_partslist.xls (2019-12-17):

SENIOR DESIGN POWER PCB
Mouser # | Mfr. # | Manufacturer | Customer # | Description | RoHS | Lifecycle | Order Qty. | Price (USD) | Ext.: (USD)
926-LM2596SX-5.0NOPB | LM2596SX-5.0/NOPB | Texas Instruments |  | Switching Voltage Regulators 150 KHZ 3A STEP-DOWN VLTG REG | RoHS Compliant |  | 1 | $4.77 | $4.77
652-SRP1038C-330M | SRP1038C-330M | Bourns |  | Fixed Inductors Ind,11x10x3.8mm,33uH 20%,4A,Shd,SMD | RoHS Compliant | New Product | 1 | $1.06 | $1.06
78-VS-50WQ04FN-M3 | VS-50WQ04FN-M3 | Vishay |  | Schottky Diodes & Rectifiers Schottky - D-PAK-e3 | RoHS Compliant |  | 1 | $0.74 | $0.74
667-EEU-FK1V681L | EEU-FK1V681L | Panasonic |  | Aluminum Electrolytic Capacitors - Radial Leaded 35VDC 680uF 20% AEC-Q200 | RoHS Compliant |  | 2 | $0.94 | $1.88
530-SS-52100-001 | SS-52100-001 | Bel |  | USB Connectors USB 2.0 R Angle Recpt Type A solder | RoHS Compliant |  | 1 | $0.44 | $0.44
845-30.602/BLU | 30.602/BLUE | Altech |  | Fixed Terminal Blocks AK300/2 PC 45Deg | RoHS Compliant |  | 2 | $1.27 | $2.54
595-INA226AIDGSR | INA226AIDGSR | Texas Instruments |  | Current & Power Monitors & Regulators Hi-Side Msmt,Bi-Dir Current/Pwr Mon | RoHS Compliant |  | 1 | $2.80 | $2.80
603-A1206FRF070R002L | PA1206FRF070R002L | Yageo |  | Current Sense Resistors - SMD 0.002 ohm 1% 100ppm | RoHS Compliant | New Product | 1 | $0.75 | $0.75
71-CRCW08054K70FKEBC | CRCW08054K70FKEBC | Vishay |  | Thick Film Resistors - SMD 1/8Watt 4.7Kohms 1% Commercial Use | RoHS Compliant By Exemption | New Product | 2 | $0.18 | $0.36
80-C0805C104J5R | C0805C104J5RACTU | KEMET |  | Multilayer Ceramic Capacitors MLCC - SMD/SMT 50V 0.1uF X7R 0805 5% | RoHS Compliant |  | 1 | $0.10 | $0.10

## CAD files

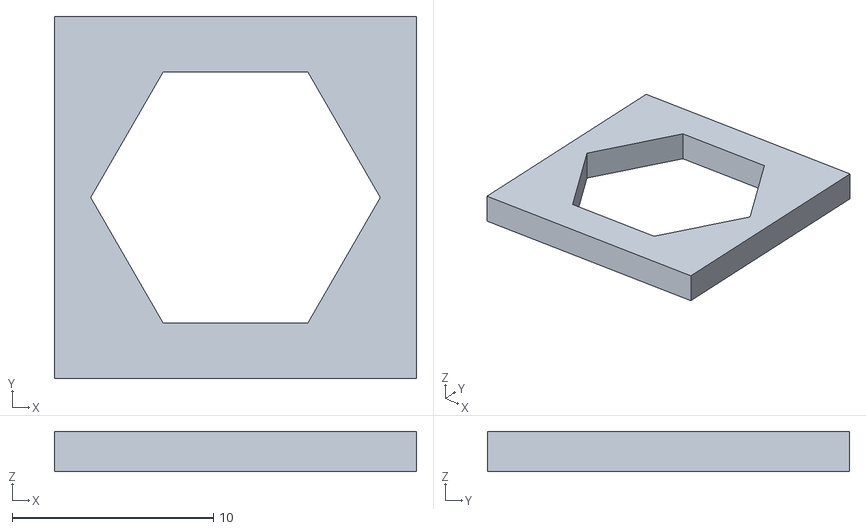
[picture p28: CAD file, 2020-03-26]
design/vehicle_cad/wheel/stl/hexMain.stl
18.0 x 18.0 x 2.00

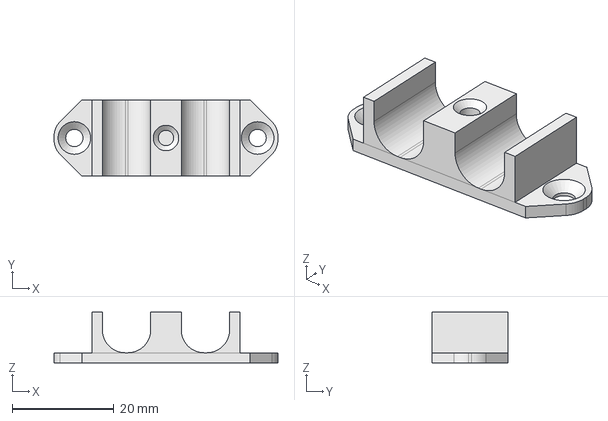
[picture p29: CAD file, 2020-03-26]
design/vehicle_cad/body/doubleDeanClampBottom.FCStd
44.0 x 15.0 x 10.0 mm

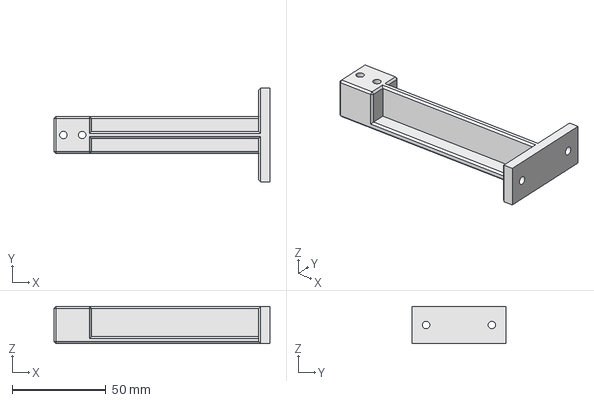
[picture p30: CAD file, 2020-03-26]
design/vehicle_cad/camera/mountTopDeckFront.FCStd
115.0 x 50.0 x 19.8 mm

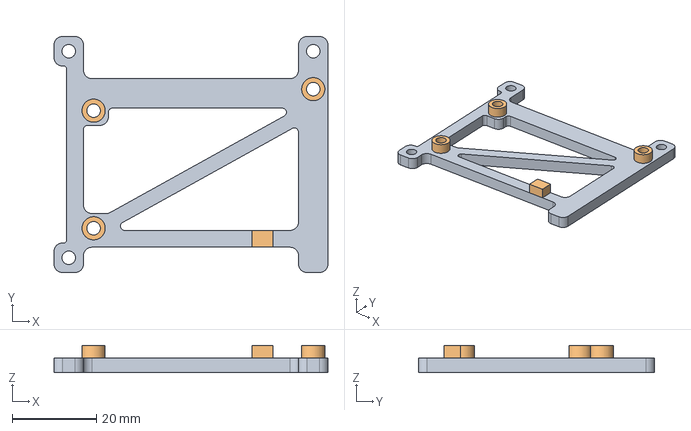
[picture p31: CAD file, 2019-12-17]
design/vehicle_cad/raspiMountArduino/raspiMountArduino.FCStd
65.0 x 56.0 x 6.50 mm

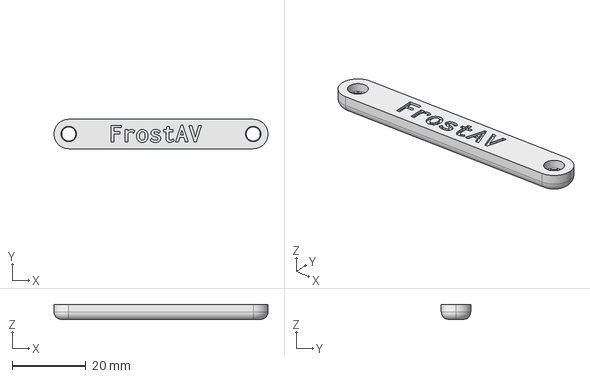
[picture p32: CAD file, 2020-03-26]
design/vehicle_cad/steering/linkage.FCStd
58.0 x 8.00 x 4.00 mm

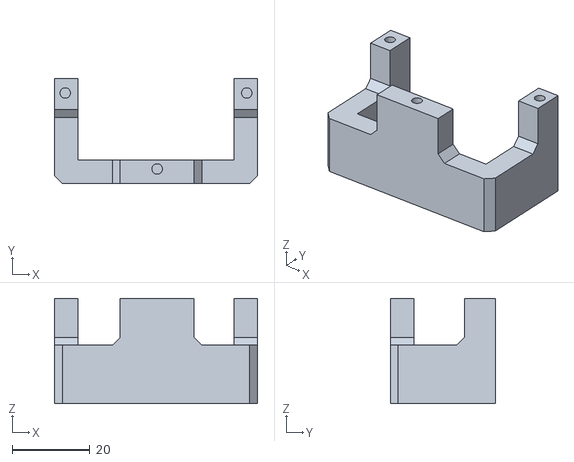
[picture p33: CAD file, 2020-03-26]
design/vehicle_cad/steering/stl/servoMount.stl
52.1 x 27.0 x 27.0

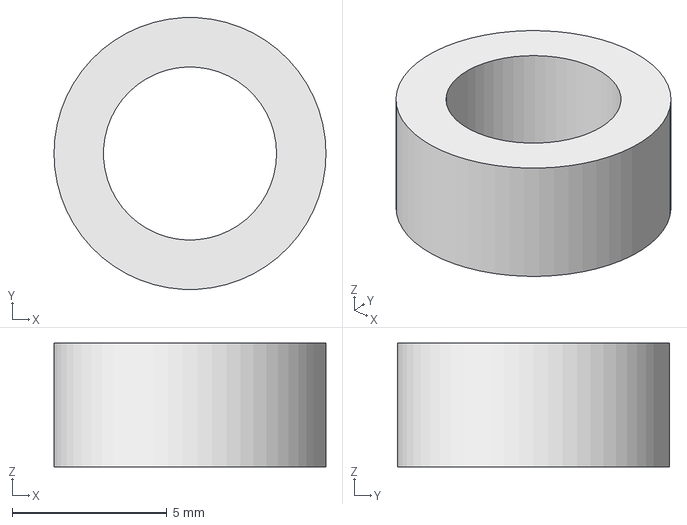
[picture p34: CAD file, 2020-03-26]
design/vehicle_cad/wheel/hubSpacer.FCStd
8.80 x 8.79 x 4.00 mm

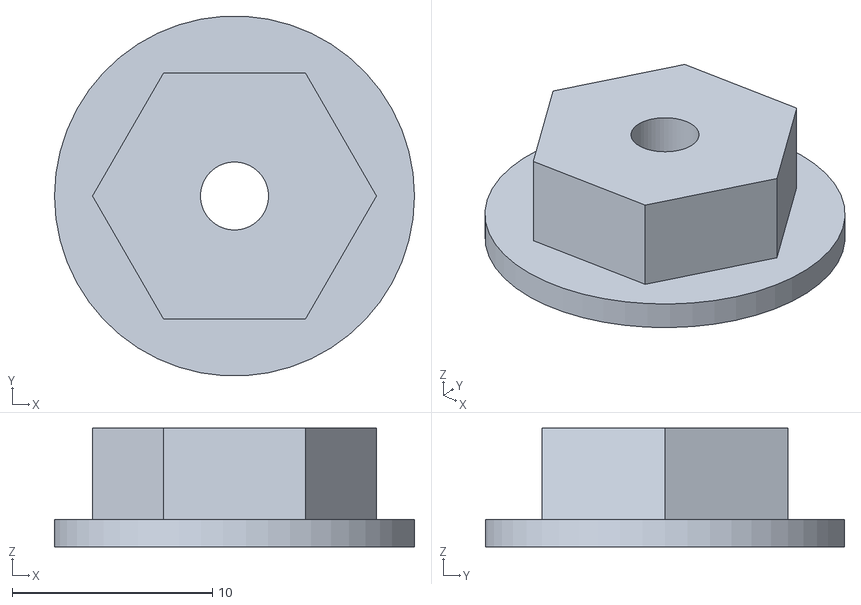
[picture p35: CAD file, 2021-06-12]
design/vehicle_cad/wheel/stl/hubHexAdapter_3mm_noD.stl
18.0 x 18.0 x 5.93

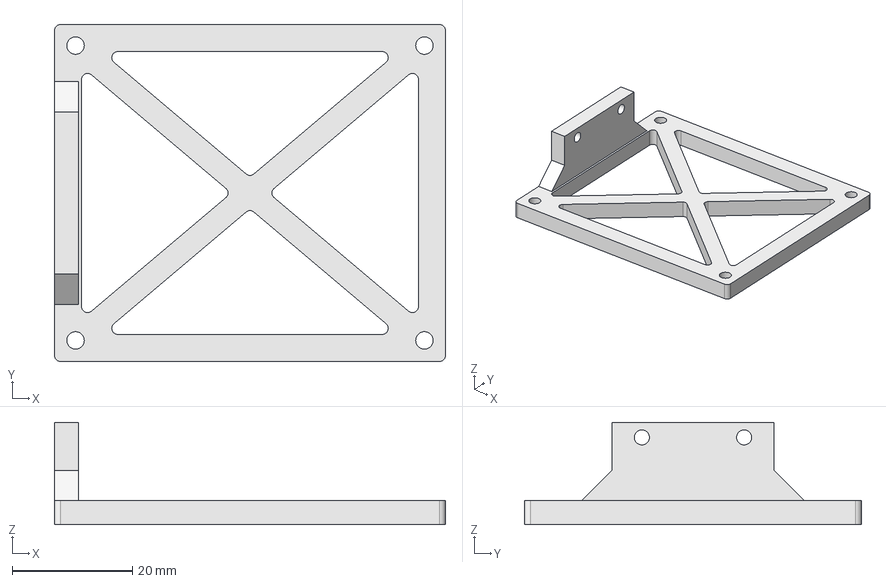
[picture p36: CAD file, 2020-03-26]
design/vehicle_cad/body/pi4BackMount.FCStd
65.0 x 56.0 x 17.0 mm

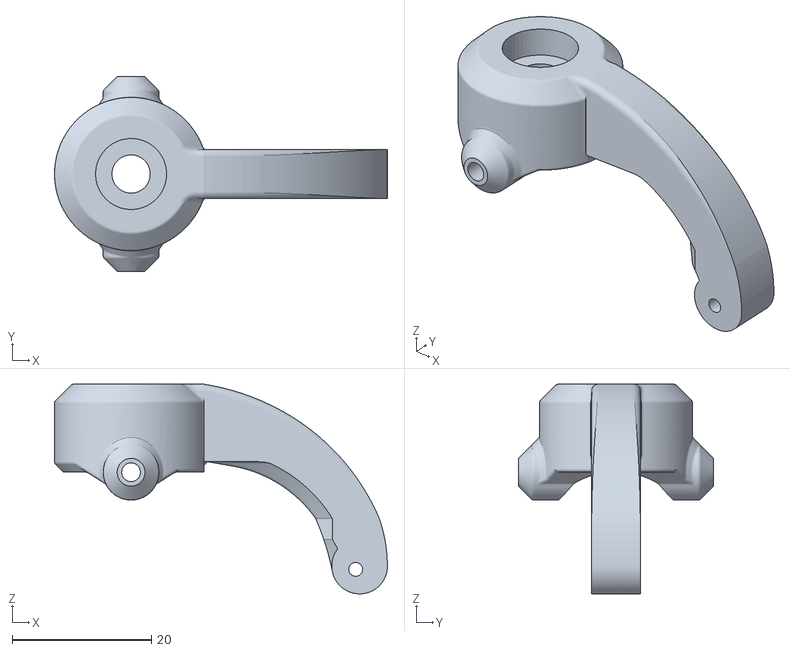
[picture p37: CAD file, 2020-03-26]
design/vehicle_cad/steering/stl/steeringBlock.stl
47.8 x 28.0 x 30.1

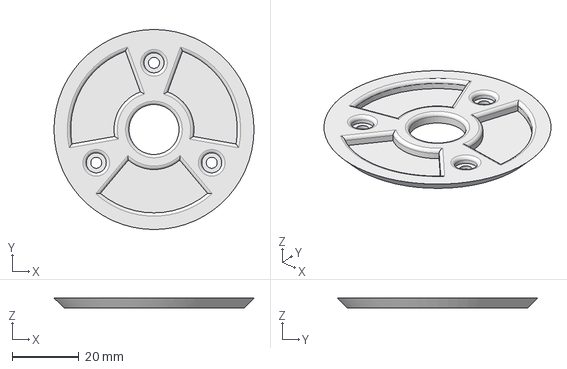
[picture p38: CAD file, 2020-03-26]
design/vehicle_cad/wheel/hubOutside.FCStd
60.0 x 60.0 x 3.00 mm

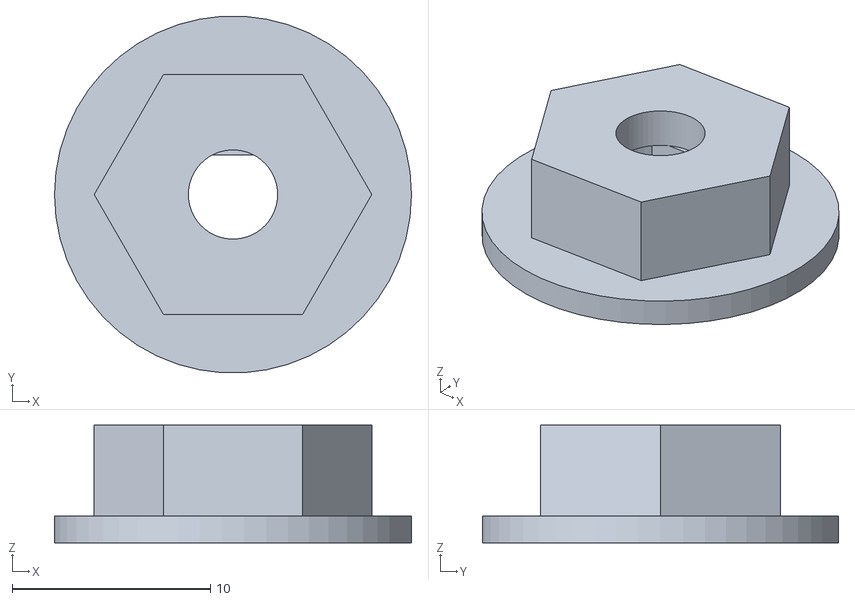
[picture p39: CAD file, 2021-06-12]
design/vehicle_cad/wheel/stl/hubHexAdapter.stl
18.0 x 18.0 x 5.93

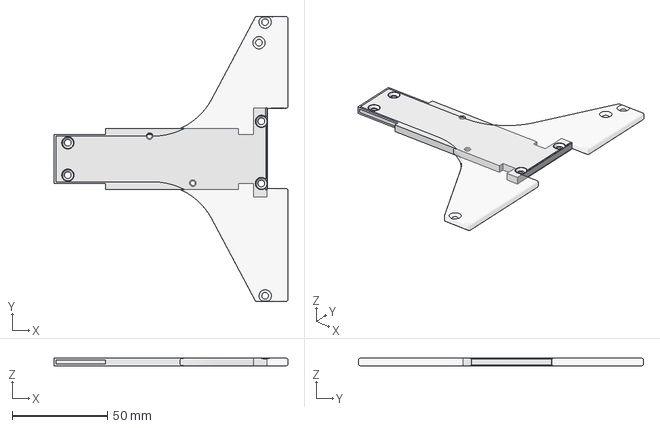
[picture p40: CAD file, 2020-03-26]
design/vehicle_cad/body/topDeckBack.FCStd
123.1 x 150.0 x 4.00 mm
Top_Deck_Rear

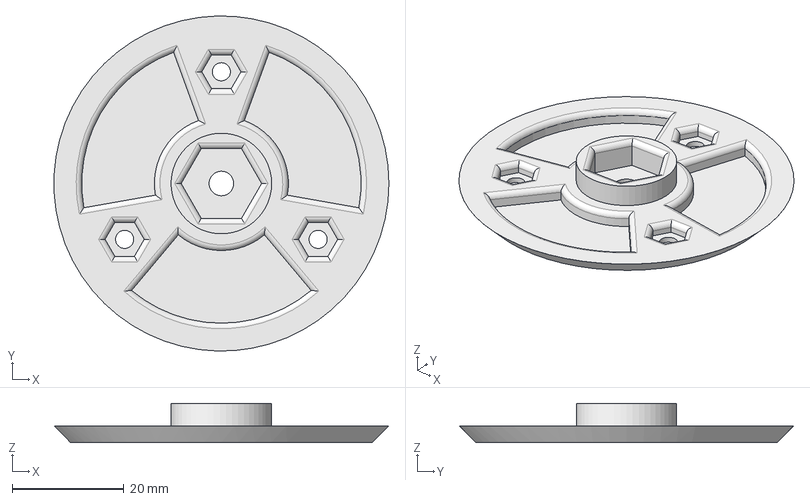
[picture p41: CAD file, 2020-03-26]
design/vehicle_cad/wheel/hubInside.FCStd
60.0 x 60.0 x 7.00 mm

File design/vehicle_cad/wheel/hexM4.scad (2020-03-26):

difference() {
     cube([11,11, 2], center=true);
     translate([0,0,-1.1]) cylinder(h=2.2, d=7, $fn = 6);
}

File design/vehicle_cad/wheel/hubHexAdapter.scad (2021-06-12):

//Units: mm

hexHeight = 4.57;

spacerHeight = 1.36;
spacerDiameter = 18;

shaftDiameter = 4.5;

dShaftEnable = true;
dShaftDiameter = 5.8;
dShaftFlatDiameter = 4.9;
dShaftInset = 3.93;

INF = 100; //arbitrarily large value


difference() {
  union() {
    translate([0,0,spacerHeight]) M7();
    Spacer();
  }

  if (dShaftEnable) {
    translate([0,0,dShaftInset]) Shaft();
    DShaft();
  }
  else {
    Shaft();
  }
}


module Shaft() {
  cylinder(h=INF, d=shaftDiameter, $fn=50);  
}

module DShaft() {
  intersection() {
    cylinder(h=dShaftInset, d=dShaftDiameter, $fn=50);
    translate([-dShaftDiameter/2,-dShaftDiameter/2,-INF/2]) cube([dShaftDiameter, dShaftFlatDiameter, INF]);
  }
}

module Spacer() {
  cylinder(h=spacerHeight, d=spacerDiameter, $fn=50);
}

module M7() {
  cylinder(h=hexHeight, d=14.2, $fn = 6);
}

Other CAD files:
design/vehicle_cad/wheel/stl/hex.stl
design/vehicle_cad/body/topDeckFront.FCStd
design/vehicle_cad/wheel/stl/hexM4.stl
design/vehicle_cad/body/doubleDeanClampMount.FCStd
design/vehicle_cad/wheel/hexMain.scad
design/vehicle_cad/body/doubleBatteryStop.FCStd
design/vehicle_cad/body/doubleDeanClampTop.FCStd
design/vehicle_cad/body/escSwitchMount.FCStd
design/vehicle_cad/body/pi4OverMotorMount.FCStd
design/vehicle_cad/body/stl/doubleBatteryStop.stl
design/vehicle_cad/body/stl/doubleDeanClampBottom.stl
design/vehicle_cad/body/stl/doubleDeanClampMount.stl
design/vehicle_cad/body/stl/doubleDeanClampTop.stl
design/vehicle_cad/body/stl/escSwitchMount.stl
design/vehicle_cad/body/stl/pi4BackMount.stl
design/vehicle_cad/body/stl/pi4OverMotorMount.stl
design/vehicle_cad/body/stl/topDeckBack.stl
design/vehicle_cad/body/stl/topDeckFront.stl
design/vehicle_cad/camera/mountTopDeckFront.stl
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

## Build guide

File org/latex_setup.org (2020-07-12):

#+latex_class: IEEEtran
#+latex_class_options: [12pt, onecolumn, journal, compsoc]
#+bind: org-latex-minted-options (("rulecolor" "gray") ("frame" "leftline") ("fontsize" "\\scriptsize") ("xleftmargin" "20pt") ("baselinestretch" "0.9"))
#+bind: org-latex-image-default-width "0.8\\linewidth"
#+options: num:t tags:nil toc:t
#+bind: org-latex-default-figure-position "H"
#+setupFile: https://fniessen.github.io/org-html-themes/setup/theme-readtheorg.setup

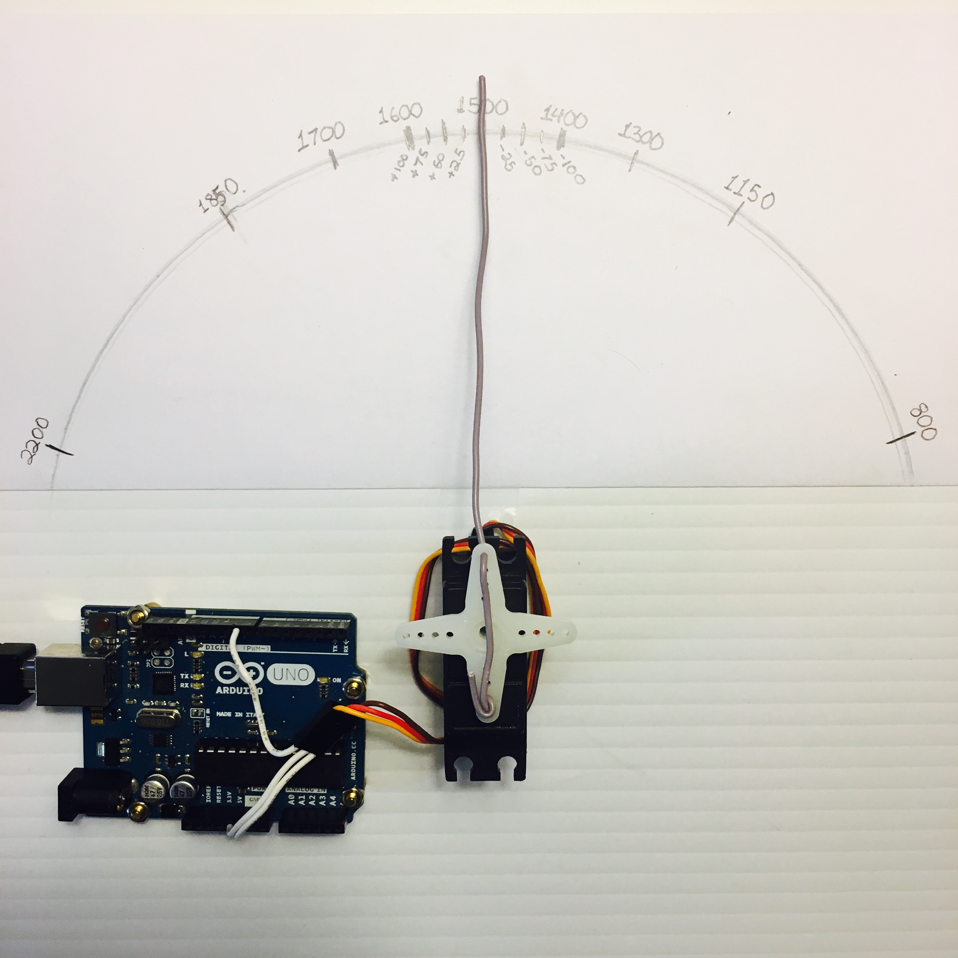
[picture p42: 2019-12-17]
org/development/1/figure/2019-11-05_pidExperimentalSetup.JPG

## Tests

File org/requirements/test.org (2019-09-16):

* Test Environment
In order to test the overall system, the car will be placed on a designated circuit.
The circuit will be created, with the lane edges defined by tape with a width less than 2 inches.
The lanes need to be wider than the width of the car.
The circuit will have at least one sign, printed onto paper and placed perpendicular to the floor.
Each corner of the circuit must be less than 45°.
There will also be automated obstacles placed onto the course which will force the car to stop, and then they will be automatically removed.

* Test requirements
The car must be able to travel in a lane, approximately parallel to it an remain within its boundaries.
If the car leaves the lane then it must promptly return to it.
When the car reaches a corner, the car must turn, following the lane boundaries consistently.
When presented with an obstacle the car must stop until it is moved away from the car's path.
The car must be able to complete a full loop of the circuit.

* Module Testing
As the car is assembled, each module will be tested individually to ensure that they function as intended.
To test the car chassis, the steering servo and motor will be individually tested to ensure that they are functional, and the car will then be tested under remote control to verify that it is functional.
For the power system, the voltage regulator will be connected to the battery, and the output voltage will be measured. The voltage must be between 4.75 and 5.25v in order to meet the USB specification. 
Next, a variable resistor will be connected to the regulator's output to simulate a load. The resistors value will be slowly decreased and the output voltage monitored.
The output voltage must remain within 0.25v to be within USB spec.

To test the servo and motor control module, the frequency of the servo and motor controller PWM outputs will be measured to ensure it is at 50 Hz. 
Next, the module will be commanded through the servo and motor controller's possible range (1ms to 2ms pulse width) and the output will be measured to ensure the correct PWM values are being sent.

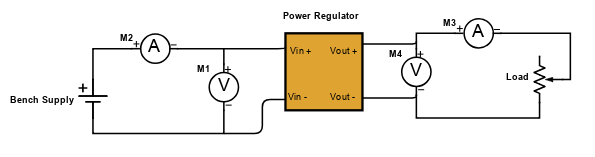
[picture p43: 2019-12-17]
org/development/1/figure/test_diagram.png

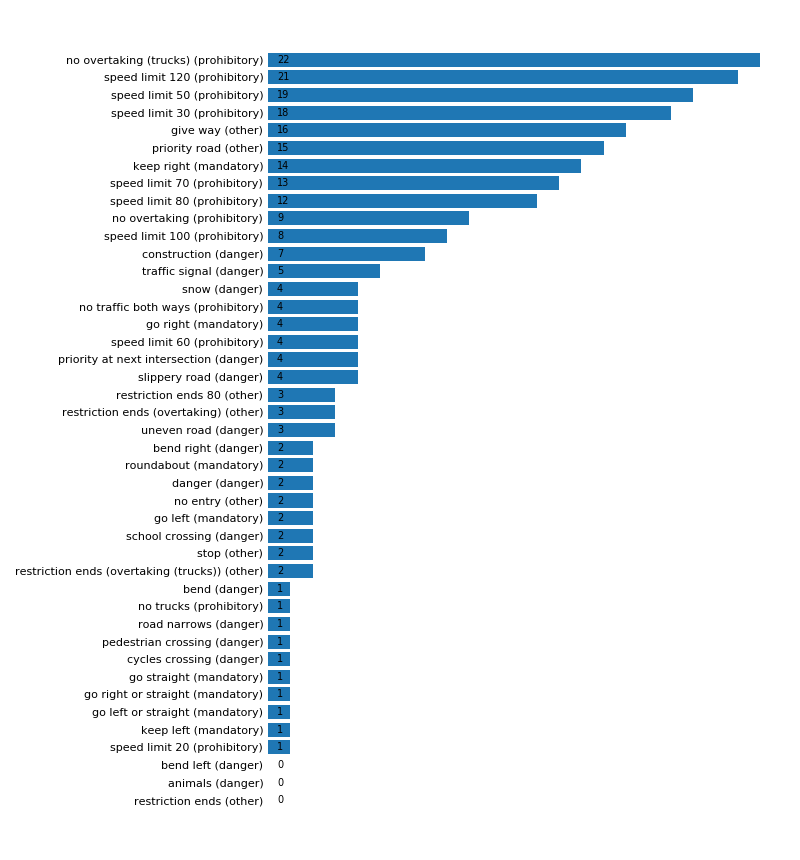
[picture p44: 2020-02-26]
server/autonomy/sign/figure/distribution_testing.png

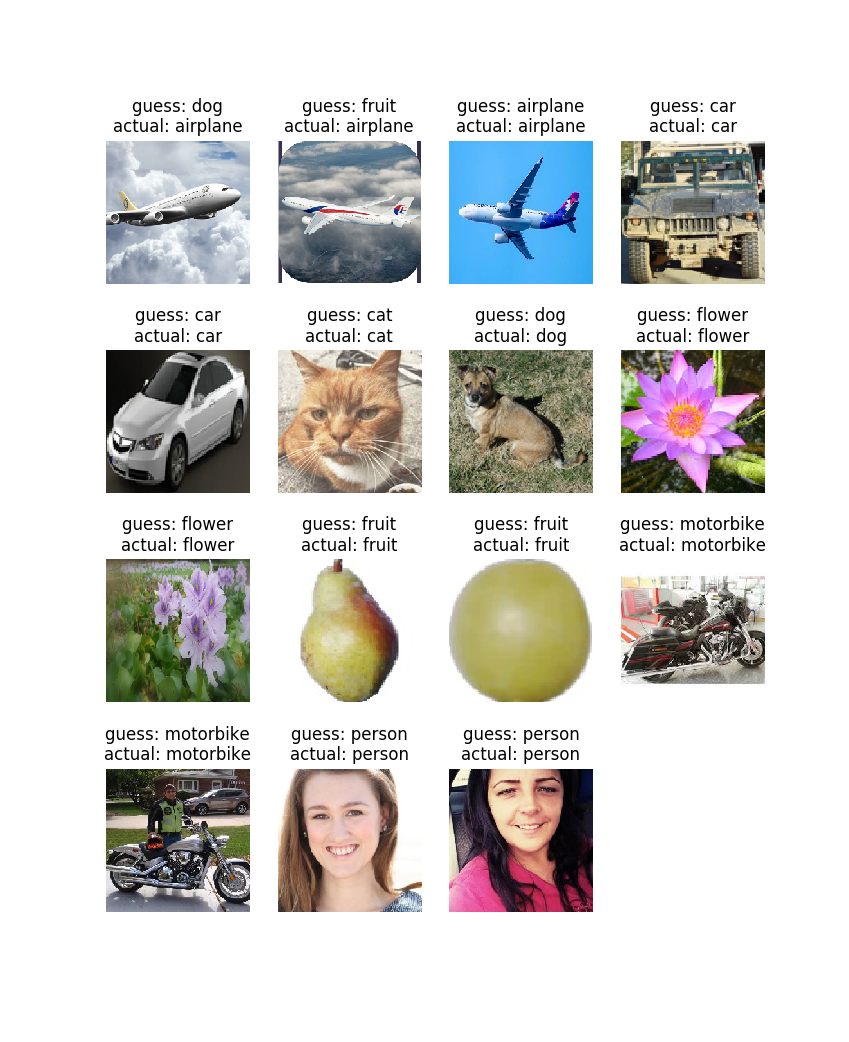
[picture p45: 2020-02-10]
research/02_TrafficSignClassification/01_SimpleObjectClassifierKerasVGG16/figure/testSetPredictions.png

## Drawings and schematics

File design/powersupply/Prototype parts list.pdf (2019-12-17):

My Shopping Cart | Mouser | https://www.mouser.com/Cart/

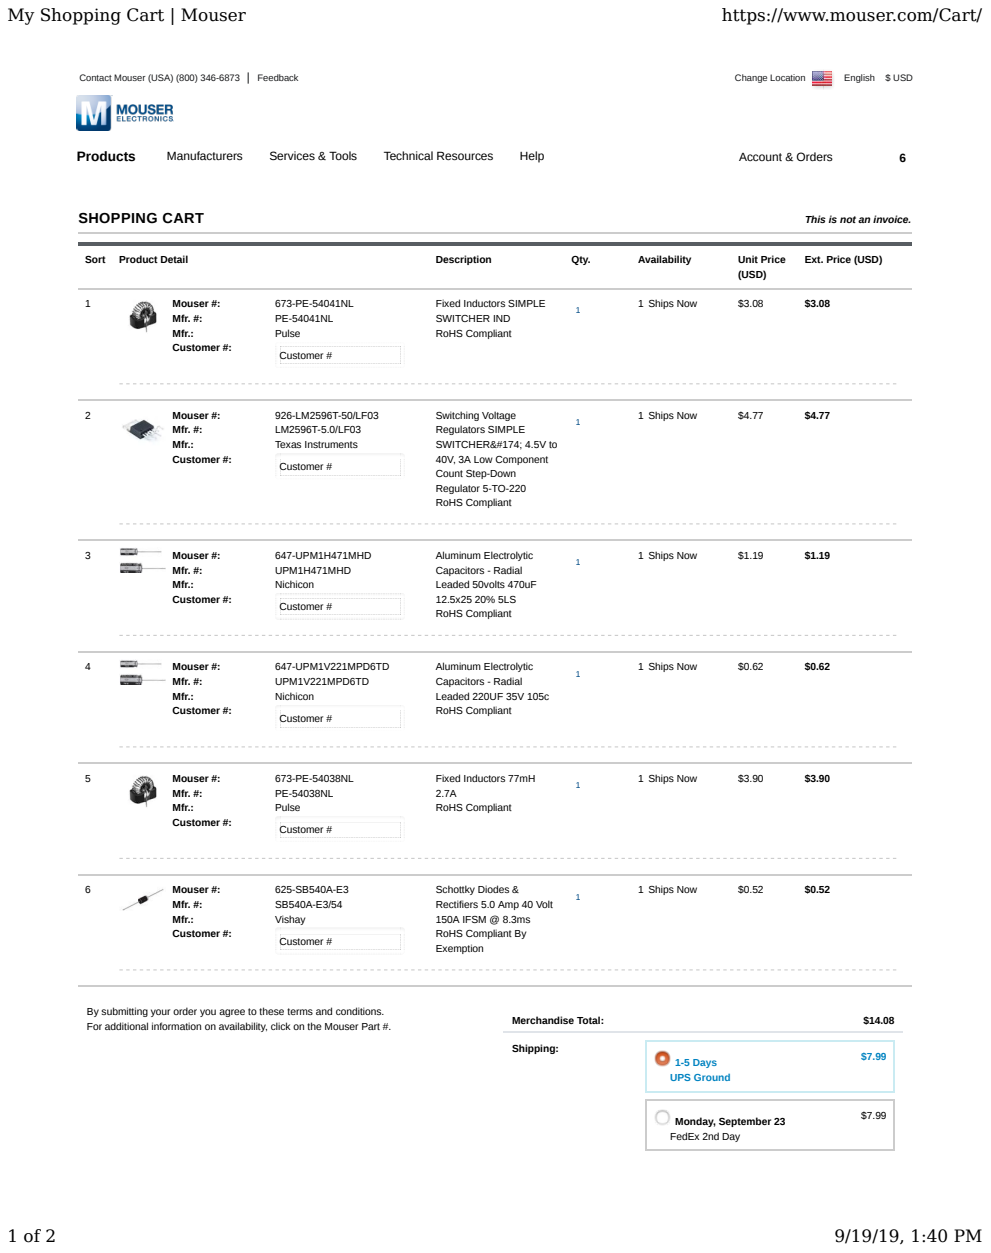
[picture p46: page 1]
Sort Product Detail; Description; Qty.; Availability; Unit Price; (USD); SHOPPING CART; This is not an invoice.; Mouser #:; Mfr. #:; Mfr.:; Pulse; Customer #:; Customer #; 1 Ships Now; Texas Instruments; 647-UPM1H471MHD; UPM1H471MHD; Nichicon; Aluminum Electrolytic Capacitors - Radial Leaded 50volts 470uF 12.5x25 20% 5LS RoHS Compliant; 647-UPM1V221MPD6TD; UPM1V221MPD6TD; Aluminum Electrolytic Capacitors - Radial Leaded 220UF 35V 105c RoHS Compliant; Fixed Inductors 77mH 2.7A RoHS Compliant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

Ext. Price (USD)

Fixed Inductors SIMPLE
SWITCHER IND
RoHS Compliant

Switching Voltage
Regulators SIMPLE
SWITCHER&#174; 4.5V to
40V, 3A Low Component
Count Step-Down
Regulator 5-TO-220

Schottky Diodes &
Rectifiers 5.0 Amp 40 Volt
150A IFSM @ 8.3ms
RoHS Compliant By
Exemption

By submitting your order you agree to these terms and conditions.

Order in the next 07:19:32 to ship today. Learn More

Tuesday, September 24
UPS 3rd Day

$12.99

Monday, September 23
UPS 2nd Day

$13.99

+ More Shipping Options

Subtotal: | $22.07
My Shopping Cart | Mouser | https://www.mouser.com/Cart/
2 of 2 | 9/19/19, 1:40 PM

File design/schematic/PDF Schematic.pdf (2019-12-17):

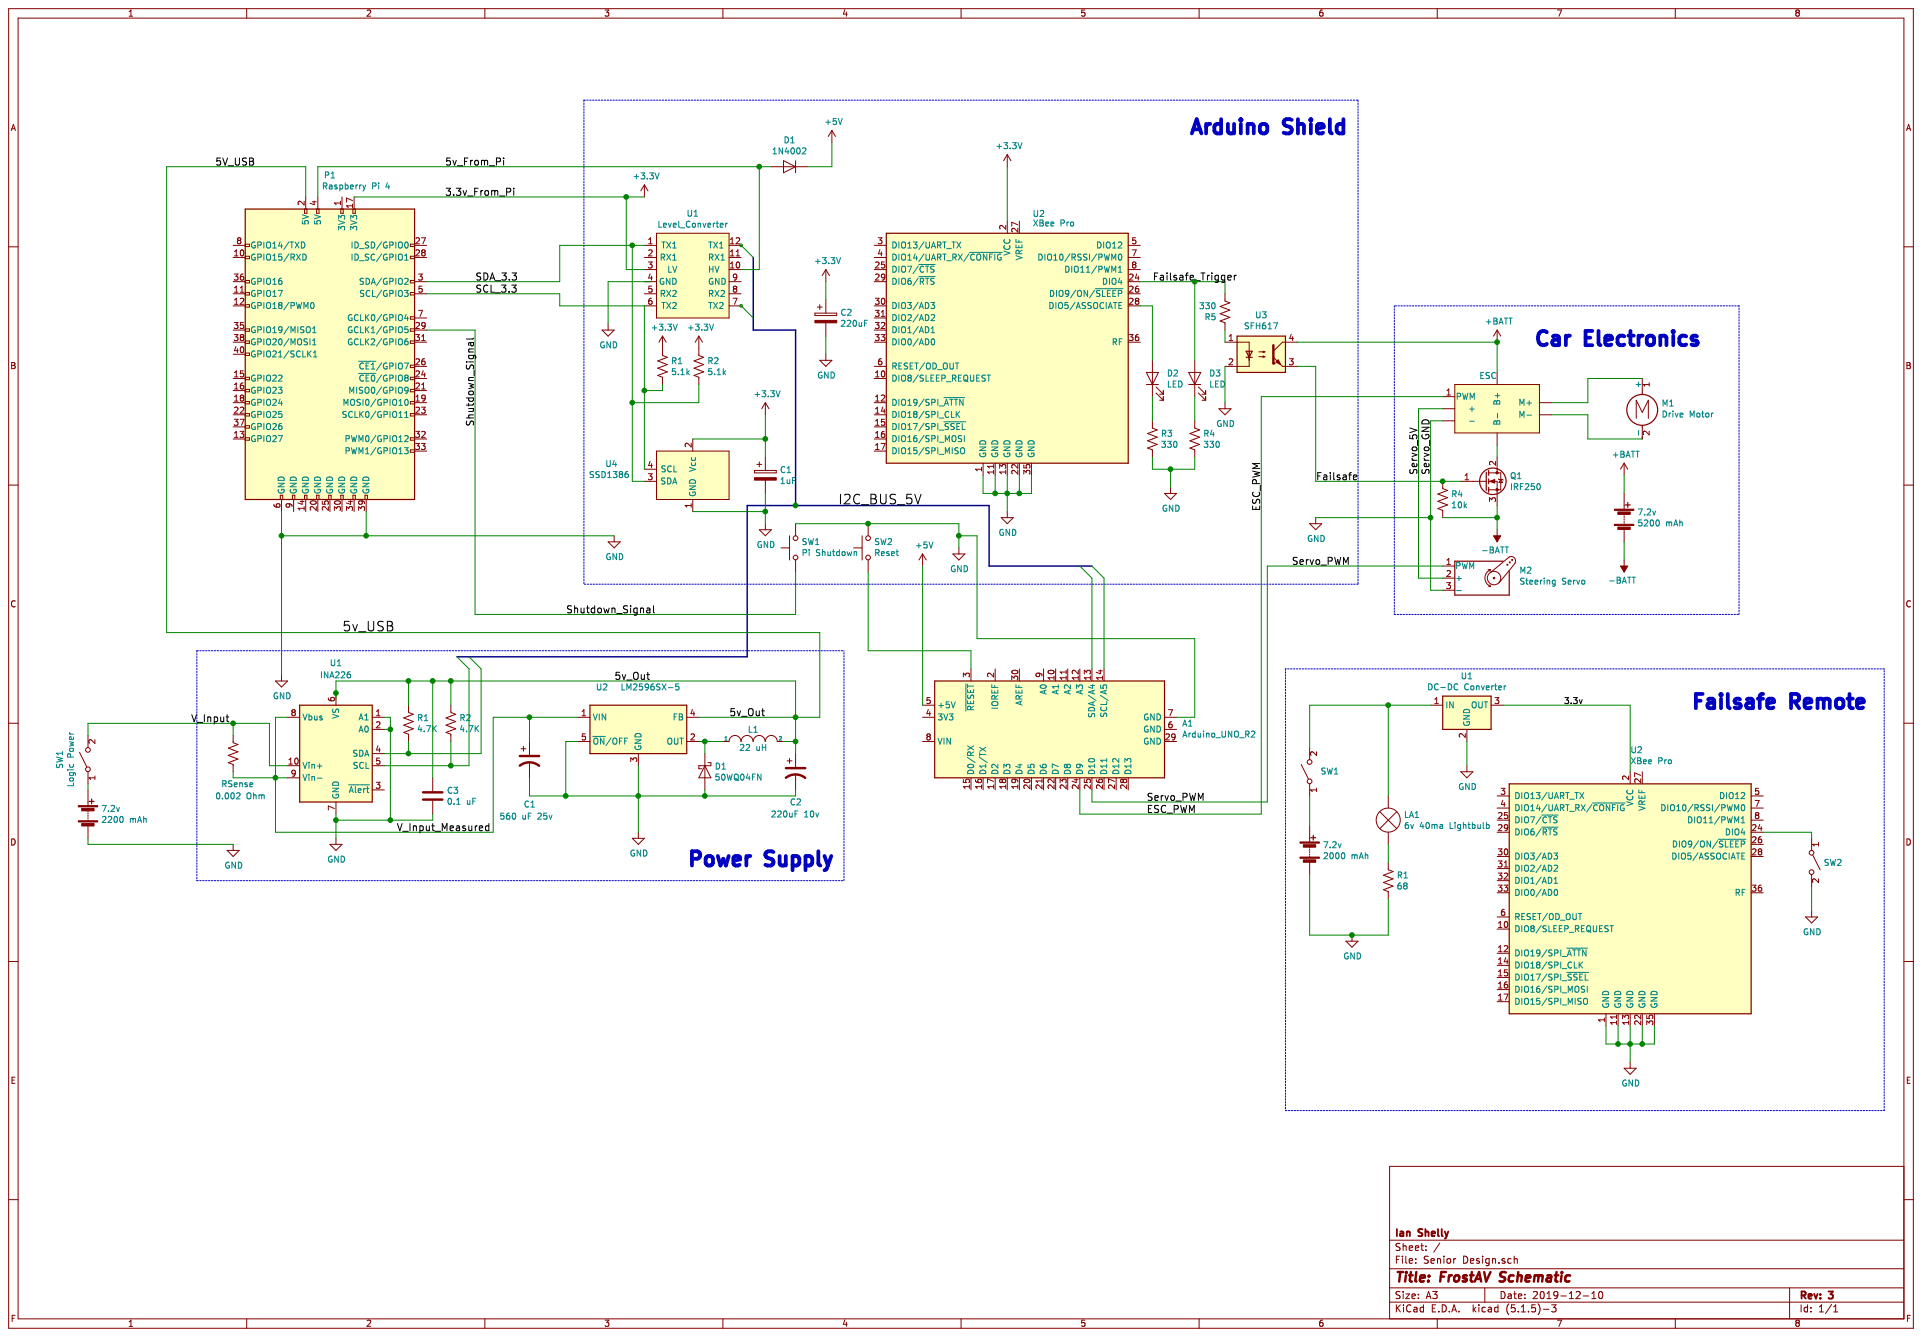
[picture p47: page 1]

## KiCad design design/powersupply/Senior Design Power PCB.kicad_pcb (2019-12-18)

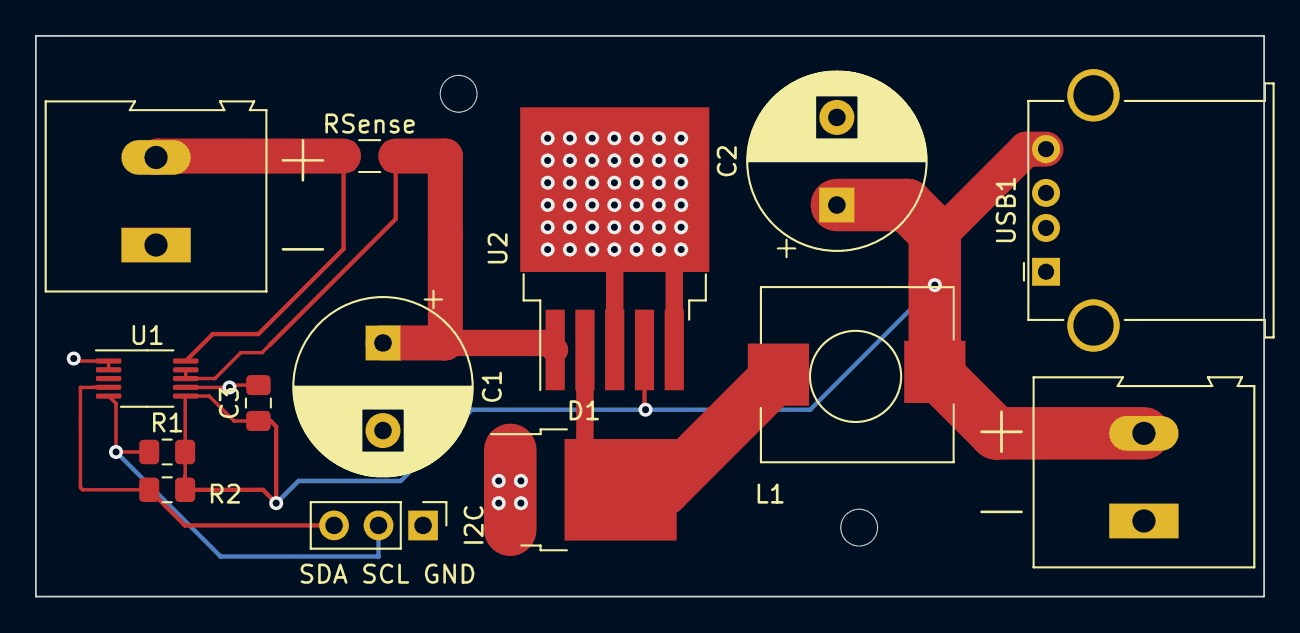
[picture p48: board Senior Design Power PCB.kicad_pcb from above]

Board: 2 copper layers, 70.1 x 32.0 mm, 13 parts (0 on the bottom side), 5 nets.

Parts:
 : TerminalBlock_Altech_AK300-2_P5.00mm
C1, C2: CP_Radial_D10.0mm_P5.00mm
C3: C_0805_2012Metric_Pad1.15x1.40mm_HandSolder
D1: TO-252-2
I2C: PinHeader_1x03_P2.54mm_Vertical
L1: SRP1038C-330M
R1, R2: R_0805_2012Metric_Pad1.15x1.40mm_HandSolder
RSense: R_1206_3216Metric_Pad1.42x1.75mm_HandSolder
U1: VSSOP-10_3x3mm_P0.5mm
U2: TO-263-5_TabPin3
USB1: USB_A_Stewart_SS-52100-001_Horizontal

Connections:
5V: C2.1, C3.1, L1.2, R1.2, R2.2, U1.6, U2.4, USB1.4
B+: C1.1, RSense.2, U1.8, U1.9, U2.1
B-: .1, C1.2, C2.2, C3.2, D1.1, D1.3, I2C.1, U1.1, U1.2, U1.7, U2.3, U2.5, USB1.1, USB1.5
SCL: I2C.2, R1.1, U1.5
SDA: I2C.3, R2.1, U1.4

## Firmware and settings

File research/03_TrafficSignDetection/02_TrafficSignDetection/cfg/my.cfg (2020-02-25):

[net]
# Testing
# batch=1
# subdivisions=1
# Training
batch=64
subdivisions=16
width=160
height=160
channels=3
momentum=0.9
decay=0.0005
angle=0
saturation = 1.5
exposure = 1.5
hue=.1

learning_rate=0.001
burn_in=1000
max_batches = 86000
policy=steps
steps=68800,77400
scales=.1,.1

[convolutional]
batch_normalize=1
filters=32
size=3
stride=1
pad=1
activation=leaky

# Downsample

[convolutional]
batch_normalize=1
filters=64
size=3
stride=2
pad=1
activation=leaky

[convolutional]
batch_normalize=1
filters=32
size=1
stride=1
pad=1
activation=leaky

[convolutional]
batch_normalize=1
filters=64
size=3
stride=1
pad=1
activation=leaky

[shortcut]
from=-3
activation=linear

# Downsample

[convolutional]
batch_normalize=1
filters=128
size=3
stride=2
pad=1
activation=leaky

[convolutional]
batch_normalize=1
filters=64
size=1
stride=1
pad=1
activation=leaky

[convolutional]
batch_normalize=1
filters=128
size=3
stride=1
pad=1
activation=leaky

[shortcut]
from=-3
activation=linear

[convolutional]
batch_normalize=1
filters=64
size=1
stride=1
pad=1
activation=leaky

[convolutional]
batch_normalize=1
filters=128
size=3
stride=1
pad=1
activation=leaky

[shortcut]
from=-3
activation=linear

# Downsample

[convolutional]
batch_normalize=1
filters=256
size=3
stride=2
pad=1
activation=leaky

[convolutional]
batch_normalize=1
filters=128
size=1
stride=1
pad=1
activation=leaky

[convolutional]
batch_normalize=1
filters=256
size=3
stride=1
pad=1
activation=leaky

[shortcut]
from=-3
activation=linear

[convolutional]
batch_normalize=1
filters=128
size=1
stride=1
pad=1
activation=leaky

[convolutional]
batch_normalize=1
filters=256
size=3
stride=1
pad=1
activation=leaky

[shortcut]
from=-3
activation=linear

[convolutional]
batch_normalize=1
filters=128
size=1
stride=1
pad=1
activation=leaky

[convolutional]
batch_normalize=1
filters=256
size=3
stride=1
pad=1
activation=leaky

[shortcut]
from=-3
activation=linear

[convolutional]
batch_normalize=1
filters=128
size=1
stride=1
pad=1
activation=leaky

[convolutional]
batch_normalize=1
filters=256
size=3
stride=1
pad=1
activation=leaky

[shortcut]
from=-3
activation=linear


[convolutional]
batch_normalize=1
filters=128
size=1
stride=1
pad=1
activation=leaky

[convolutional]
batch_normalize=1
filters=256
size=3
stride=1
pad=1
activation=leaky

[shortcut]
from=-3
activation=linear

[convolutional]
batch_normalize=1
filters=128
size=1
stride=1
pad=1
activation=leaky

[convolutional]
batch_normalize=1
filters=256
size=3
stride=1
pad=1
activation=leaky

[shortcut]
from=-3
activation=linear

[convolutional]
batch_normalize=1
filters=128
size=1
stride=1
pad=1
activation=leaky

[convolutional]
batch_normalize=1
filters=256
size=3
stride=1
pad=1
activation=leaky

[shortcut]
from=-3
activation=linear

[convolutional]
batch_normalize=1
filters=128
size=1
stride=1
pad=1
activation=leaky

[convolutional]
batch_normalize=1
filters=256
size=3
stride=1
pad=1
activation=leaky

[shortcut]
from=-3
activation=linear

# Downsample

[convolutional]
batch_normalize=1
filters=512
size=3
stride=2
pad=1
activation=leaky

[convolutional]
batch_normalize=1
filters=256
size=1
stride=1
pad=1
activation=leaky

[convolutional]
batch_normalize=1
filters=512
size=3
stride=1
pad=1
activation=leaky

[shortcut]
from=-3
activation=linear


[convolutional]
batch_normalize=1
filters=256
size=1
stride=1
pad=1
activation=leaky

[convolutional]
batch_normalize=1
filters=512
size=3
stride=1
pad=1
activation=leaky

[shortcut]
from=-3
activation=linear


[convolutional]
batch_normalize=1
filters=256
size=1
stride=1
pad=1
activation=leaky

[convolutional]
batch_normalize=1
filters=512
size=3
stride=1
pad=1
activation=leaky

[shortcut]
from=-3
activation=linear


[convolutional]
batch_normalize=1
filters=256
size=1
stride=1
pad=1
activation=leaky

[convolutional]
batch_normalize=1
filters=512
size=3
stride=1
pad=1
activation=leaky

[shortcut]
from=-3
activation=linear

[convolutional]
batch_normalize=1
filters=256
size=1
stride=1
pad=1
activation=leaky

[convolutional]
batch_normalize=1
filters=512
size=3
stride=1
pad=1
activation=leaky

[shortcut]
from=-3
activation=linear


[convolutional]
batch_normalize=1
filters=256
size=1
stride=1
pad=1
activation=leaky

[convolutional]
batch_normalize=1
filters=512
size=3
stride=1
pad=1
activation=leaky

[shortcut]
from=-3
activation=linear


[convolutional]
batch_normalize=1
filters=256
size=1
stride=1
pad=1
activation=leaky

[convolutional]
batch_normalize=1
filters=512
size=3
stride=1
pad=1
activation=leaky

[shortcut]
from=-3
activation=linear

[convolutional]
batch_normalize=1
filters=256
size=1
stride=1
pad=1
activation=leaky

[convolutional]
batch_normalize=1
filters=512
size=3
stride=1
pad=1
activation=leaky

[shortcut]
from=-3
activation=linear

# Downsample

[convolutional]
batch_normalize=1
filters=1024
size=3
stride=2
pad=1
activation=leaky

[convolutional]
batch_normalize=1
filters=512
size=1
stride=1
pad=1
activation=leaky
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

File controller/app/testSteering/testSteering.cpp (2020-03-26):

#include <avr/io.h>
#include <stdint.h>
#include <stdlib.h>

#include "car.hpp"

int main() {
    car::start();
	while(1) {
        for (uint16_t i = car::servo::microsBounds.lower; i <= car::servo::microsBounds.upper; i += 10) {
            car::servo::setMicros(i);
            _delay_ms(20);
        }
        for (uint16_t i = car::servo::microsBounds.upper; i >= car::servo::microsBounds.lower; i -= 10) {
            car::servo::setMicros(i);
            _delay_ms(20);
        }        

    }
}

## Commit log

2019-09-20 Removed implementation-specific material and reformatted.
2019-09-23 Added Stage 1: Base with Implementation Diagram.
2019-09-30 Finished first draft of stage 1 development specification.
2019-10-24 Added Camera to Control diagram.
2019-10-31 Added power supply design files
    [Parts List.ods, Parts List.xls, Senior Design Power PCB.kicad_pcb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]
2019-10-31 Added power supply schematic images
2019-10-31 Added powersupply section
2019-10-31 added buck diagram
2019-11-03 Register-level servo sweeping + makefile.
2019-11-03 resize buck converter diagram
2019-11-03 edited power supply
2019-11-04 Broadened sweeping range for servo PID experiment.
2019-11-04 Initial Pid. Tests pass with CxxTest and g++17
2019-11-04 Initial Clamp. Tests pass with CxxTest and g++17
2019-11-04 Changed clamping conditionals to ternary operator. Static member function is not working.
2019-11-04 Switched ordering of bounds.
2019-11-04 Servo controlled via USART, with bounds clamping, to avoid an input outside the range of the servo bounds.
2019-11-04 added new partslist
    [Parts List (old).ods, Parts List (old).xls, final_partslist.xls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]
2019-11-04 fixed partslist
    [Parts List (old).ods, Parts List (old).xls, Parts List.ods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]
2019-11-04 Fixed image widths for power schematics. Checked spelling for Power sections.
2019-11-05 Fixed static members causing device to not respond, by making them constexpr as well as the contructors they call.
2019-11-05 Implemented PID experimental setup. The current input error is not actual error and needs real feedback error.
2019-11-05 Layed out each section for the steering pid documentation.
2019-11-05 Fixed initial servo pulse width not clamping.
2019-11-05 added i2c library
2019-11-06 Finished steering servo PID documentation.
2019-11-06 I2C is now responding to master
2019-11-06 recieving i2c message
2019-11-07 fixing pwm
2019-11-07 i2c working, has control
2019-11-07 added logic for i2c
2019-11-07 fixing i2c data processing
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2019-11-07 i2c working, servo fast enough
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2019-11-08 Added live camera script.
2019-11-24 Two sweeping servos with independent position control
2019-11-24 Refactored out Cycles namespace for timer cycle calculations. Removed 'clockFrequency' variable from application code since it is defined already as F_CPU.
2019-11-27 Created 'dual_servo' and 'car' singletons to abstract timer register code. Updated app files to use these new abstractions.
2019-11-29 Added 'multi_esc_servo' to test sweeping esc and servo.
2019-12-03 Added python app files that track blue tape lanes with gain17 raw files '../raw/*gain17'
2019-12-03 Removed powersupply 'cache' file
2019-12-05 Added Raspberry Pi mount for Arduino FreeCad design
    [raspiMountArduino.FCStd, raspiMountArduino.stl]
2019-12-05 Added rounded corners
    [raspiMountArduino.FCStd, raspiMountArduino.stl]
2019-12-05 Added built-in standoffs for Arduino
    [raspiMountArduino.FCStd, raspiMountArduino.stl]
2019-12-05 Moved I2C_slave to common. Fixed header error
2019-12-05 Fixed I2C error caused by optimization (Os). Now using optimization 03.
2019-12-08 Templatized Clamp and Bounds
2019-12-10 Fixed int16 truncation for servo range for 'full' app. Added aditional helper functions.
2019-12-12 added overall schematic
    [Senior Design Power PCB.sch, schematic.sch]
2019-12-12 added full schematic
    [schematic.sch]
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2019-12-17 added power supply section
    [Senior Design Power PCB.kicad_pcb]
2019-12-17 updated power supply section
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2019-12-17 updated power supply schematic
2019-12-17 fixed power supply schematic
    [Senior Design Power PCB.sch]
2019-12-18 Began radial image processing research. Currently able to unwrap radial images.
2020-02-13 Added logger to log information about a new training 'run' in a run directory
    [log.csv]
2020-02-14 Added modelSummary to logging. Fixed 'common' import error by deleting import. Added BatchNormalization layer.
    [log.csv]
2020-02-14 Made a before and after of batch with preprocessing. Cleaned up README.org heading structure.
    [log.csv]
2020-02-20 Added classifier training run. Added resource link to sign detection.
    [log.csv]
2020-02-20 Refactored research directory structure
    [yolov3-tiny.cfg]
2020-02-25 Yolo-Lite Model Detecting with 30% maP
    [my-lite.cfg, my.cfg]
2020-02-26 Added yolov3-tiny-prn config
    [yolov3-tiny-prn.cfg]
2020-03-05 Started 04_NodalLaneDetection Basic Node interaction between functional filtering steps for lane detection. Debugging functions (e.g. plotting) can be tied in to the nodal system.
2020-03-15 Fixed crashing when no hough lines are generated. Now the EdgeSegmentator will gauranteed return a list (possibly empty). Also, extracted from the EdgeSegmentator file, the functionality to display l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
2020-03-16 Calibrated tape-line color range in LAB color space instead of HSV. Nodes have built in distribution instead of using a distributor object.
2020-03-26 Made new printable parts - steering linkages - double battery stop - double dean connector clamp - ESC Switch Mount - RPi4 Mount - Front & Back Top Decks (now skinnier to provide easier access to bot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
    [doubleBatteryStop.FCStd, doubleBatteryStop.stl, doubleDeanClampBottom.FCStd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]
2020-03-26 Added two apps. One app for splicing i2c data and controlling the vehicle, and one for testing steering.
2020-03-26 Started Tracking FrostServer. Currently, the front-end includes FPV video streaming and linux sensor data plotting.
2020-03-29 Improved UI. Gave Node state output. Refactored the lane detection system. Simplified threading for opencv camera.
2020-03-29 Fixed GUnicorn error unable to open camera. Changed video "source" from '0' OR 'sys.argv[1]' to only '0' (indicating /dev/video0).
    The "source" of the camera, before, was sys.argv[1] if sys.srgv[1]
    existed, otherwise it was /dev/video0. This is fine when prototyping
    with Flask, since we typically do not include a parameter for
    sys.argv[1] (when running 'python __init__.py <could put source
    here>'). However, gunicorn DOES have command-line arguments and
    sys.argv[1] is NOT a video source. For this reason, it couln't read
    frames from sys.argv[1].
2020-04-01 Frame & Annotation Selection.
    - Fixed inability for gunicorn to handle more than 1 client by
    increasing --threads to 10 (as opposed to default 1)
    - Added a sidebar for the camera stream that allows the user to select
    the frame and annotations to be displayed.
    - the frame Subject now starts a thread for itself to capture opencv
    frame, and it starts a thread for each of its observers. Each observer
    thread uses the subject's current frame. This is meant to allow frames
    to be captured and processed seperately.
    - Refactored modules running as scripts (frame subject, laneModel).
    - A frame Model now exists to keep track of Nodes that have been added
    to it. Example usage: laneModel.py
2020-04-04 Added Frame Modifiers.
    - Added ROI parameters for constraining the bouding region.
    - Added 'if <list> is not None' in a few places to fix 'None is not iterable' error
    - Attempted to use CLAHE (not working any better for LAB color space)
    - Added Cross Track Error calculator
2020-04-09 Signs detected @ 1 Frame Per 5 Seconds
    [my-lite.cfg]
2020-04-10 Logging FPS of sign detection.
    [my-lite.cfg]
2020-04-22 Lane Error, Sign detection, and basic steering & sign reaction.
2020-04-22 Added Power Supply Description & Render Image
2020-04-22 Added top-level schematic description & image
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2020-04-22 Replaced schematic pdf with png
2020-04-22 Added March 2020 3d printables
2020-04-22 Added 3D printed chassis section
2020-05-19 button categories deduced from models
2020-07-12 Renamed directories
    [doubleBatteryStop.FCStd, doubleBatteryStop.stl, doubleDeanClampBottom.FCStd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]
2020-08-26 Model is no longer tied to concept of Framers and Annotators
2020-08-29 Created top-level model in 'model' directory (__init__.py)
    [my-lite.cfg]
2020-09-04 Extracted 'frame' package as 'nodal' to a separate repository
2020-11-16 Cleaned javascript button panel creation
2021-06-12 Made SCAD hub hex adapter to attach wheels to D shaft
    [hubHexAdapter.scad, hubHexAdapter.stl, hubHexAdapter_3mm_noD.stl]
